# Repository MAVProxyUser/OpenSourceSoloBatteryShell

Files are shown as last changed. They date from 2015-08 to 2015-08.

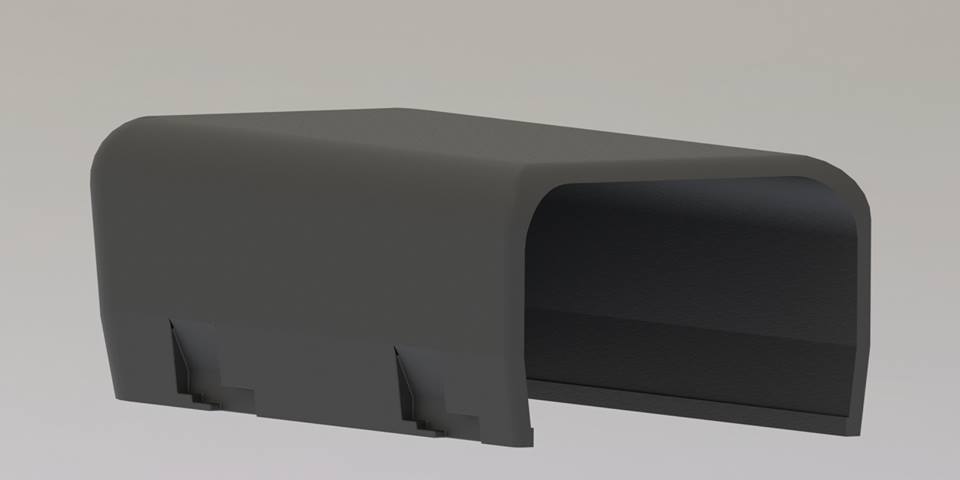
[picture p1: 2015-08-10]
11866417_101588743529360_5121034654830992906_n.jpg

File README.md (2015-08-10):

# OpenSourceSoloBatteryShell
This shell by Soloing accompanies the post: https://www.facebook.com/groups/363840837156620/permalink/375658862641484/
Soloing can be found on Rcgroups on the Solo Owners Thread - http://www.rcgroups.com/forums/showthread.php?t=2391450

If you wish to create your own Solo Battery from a common LiPo The build instructions are as follows:

SoloIng Battery Mod

(Soloing from RCGgroups)
I opened up a Solo battery, and just want to share my findings. This is my first ever write-up, so be nice. : )
- I cracked the battery open. The case consists of two pieces. Top and Bottom. They are just snapped together. No glue and no screws. It was really hard to open and a huge PITA. Kind of like trying to open some of the hard plastic blister packs, you have nowadays for many retail items. : )
- Once you take the top part of the case off, you can see the actual "battery" - the LiPo cells. The cells are taped to the bottom piece of the case, with double side tape.
- The "brain" of the battery, the board, "sits" next to the cells. It is not glued in place, or anything like that. It just sits there. Not lose though. It is held in place by the top and bottom case pieces.
- On the little board at the end of the battery, you will find the ON/OFF switch and the LED indicator, for charge and capacity. Same with this little board. It is held in place by the top and bottom case pieces. No glue, screws or tape.
- Once you open the case, you can take both boards out. However, the LED board is still attached to the main board, and the main board is still attached to the battery via the power leads (positive and negative), and the balancing wires.
- The next step was trying to get the battery itself (LiPo cells) out of the case. This was not to an easy task, as I feared to damage the cells. If I remember correctly, I used a butter knife to slowly pry the cells out of the case. They are attached with double sided tape to the bottom piece of the case.
So far, so good. Now you have the top and bottom piece of the case and the cells with the boards attached to it.
- The next thing I did was, de-solder the positive and negative wires from the battery, and unplug the balance wires from the board. (The balance leads are just connected via a plug to the board. You can just pull the plug out).
- Once I did that, I installed Anderson Power Poles to the wires (the ones coming from the board), and soldered wires to the battery, in order to install my APP connectors. I love those Anderson Power Poles btw... : )
- At this point I was able to finally hook up my OWN battery to board, and plug the board into the Solo! YEAH!
- The only thing left to do with the battery, is to take the balance wires off and replace them with any balancing tab of your choice. Since all my batteries come with JST-XH balance connectors, I soldered a JST-XH balance lead to the battery.
- Now you have the ORIGINAL Solo cells with a connector and balance tab, of your choice. Of course you can use the modified Solo battery in the Solo, or any other RC application of your choice! (in other words, the battery (cells) itself does not go to waste when you open the case!!!
- Now it was time to put my "creation" to the test. I plugged the board into the Solo, then attached my OWN battery and pressed the power button. BAM! The Solo powers ON! Great! After around 10 seconds though, the Solo started peeping! WTH? It turns out, that you also NEED to attached the balance leads to the board. If you don't do that, you will not be able to fly.
- Since the JST-XH balance leads from my batteries obviously don't fit into the board, I had to make an adapter. JST-XH to - whatever the connector is on the board. I have no idea what connector that is, but I just used the original balancing wires from the Solo battery. Even though I hate soldering, I managed to make an adapter, ha ha.
- Having done that, I was finally able to power on the Solo, using my own battery, without having the Solo giving me trouble!
- I took it outside and went for a spin. Everything seemed normal!
- Only thing left to do is to set the capacity in Mission Planner to whatever mAh you use...
I hope my write-up is easy to understand?! If you have any question, feel free to ask!
Thanks.

SoloIng Battery Mod

SoloIng Battery Mod

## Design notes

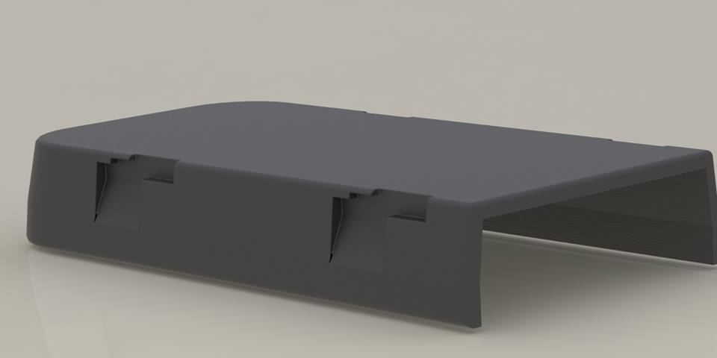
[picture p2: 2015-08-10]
11880404_101588693529365_1767681329094682993_n.jpg

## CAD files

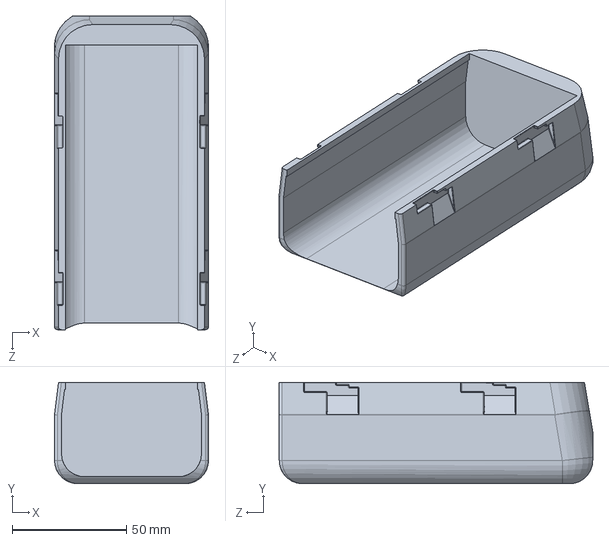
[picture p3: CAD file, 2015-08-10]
Battery Cover.SLDPRT
67.5 x 44.5 x 137.4 mm

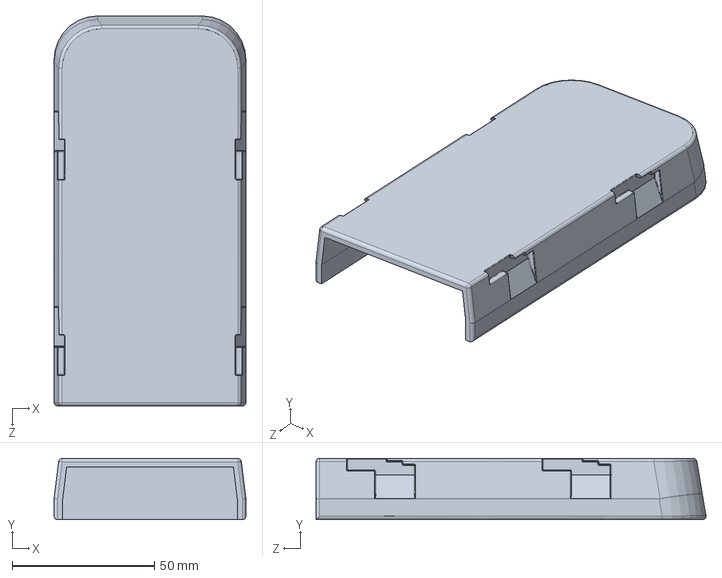
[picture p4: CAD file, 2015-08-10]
Battery Holder.SLDPRT
67.5 x 21.6 x 137.2 mm

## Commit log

2015-08-10 Public commit of the gracious work by Soloing of RCGroups Forum. This helps facilitate "Open Source" Solo Battery replacements.
    [Battery Cover.SLDPRT, Battery Holder.SLDPRT]
2015-08-10 Add art images of the rendered battery tray
